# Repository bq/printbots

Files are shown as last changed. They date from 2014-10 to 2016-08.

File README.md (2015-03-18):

<table>
<tr>
<td>

</td>
</tr>
</table>

# BQ Printbots

In this repository you will find the source files for the **bq printbots**. If you are missing something, please do not hesitate to [file an issue on github](https://github.com/bq/printbots/issues)

En este repositorio se encuentran los ficheros fuente de los **Printbots de bq**. Si echas en falta algo, no dudes en [rellenar una tarea en github](https://github.com/bq/printbots/issues)

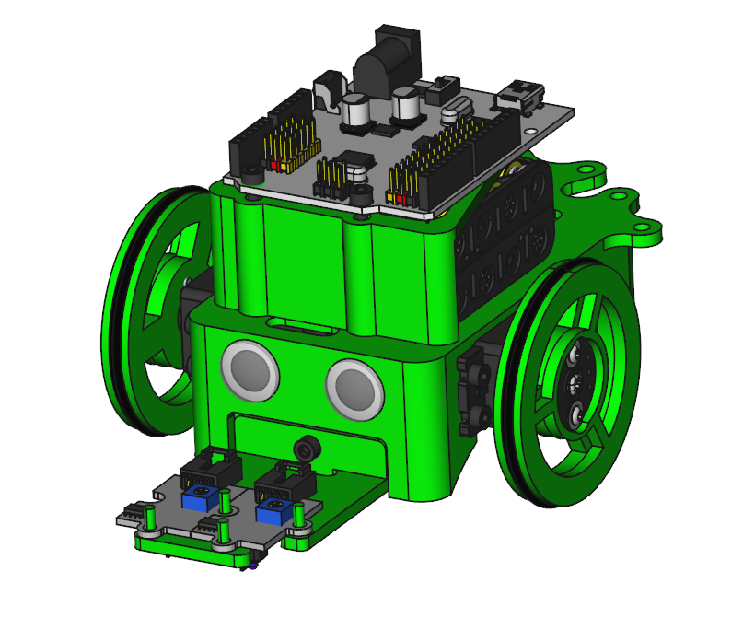
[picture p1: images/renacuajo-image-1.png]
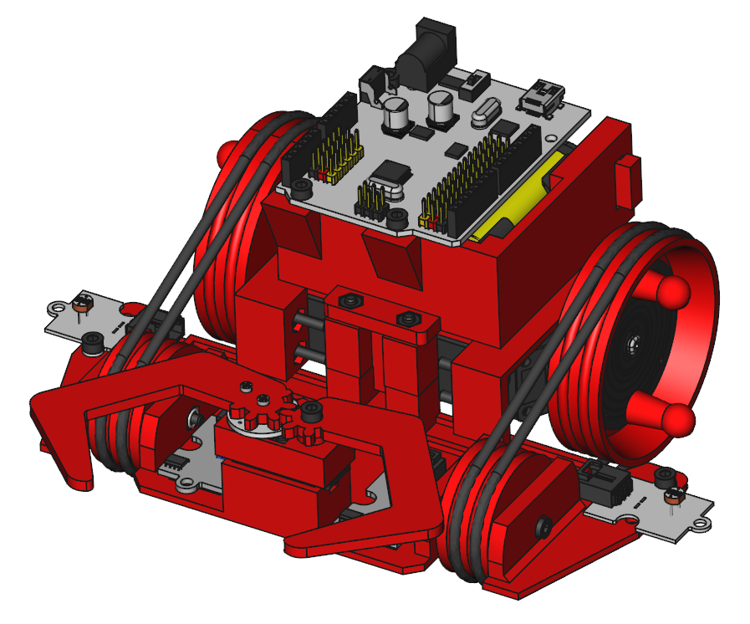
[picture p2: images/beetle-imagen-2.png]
 | 
:-------------: | :-------------:
[Printbot Renacuajo](http://diwo.bq.com/montaje-del-printbot-renacuajo/)|[Printbot Beetle](http://diwo.bq.com/product/kit-printbot-beetle/) 

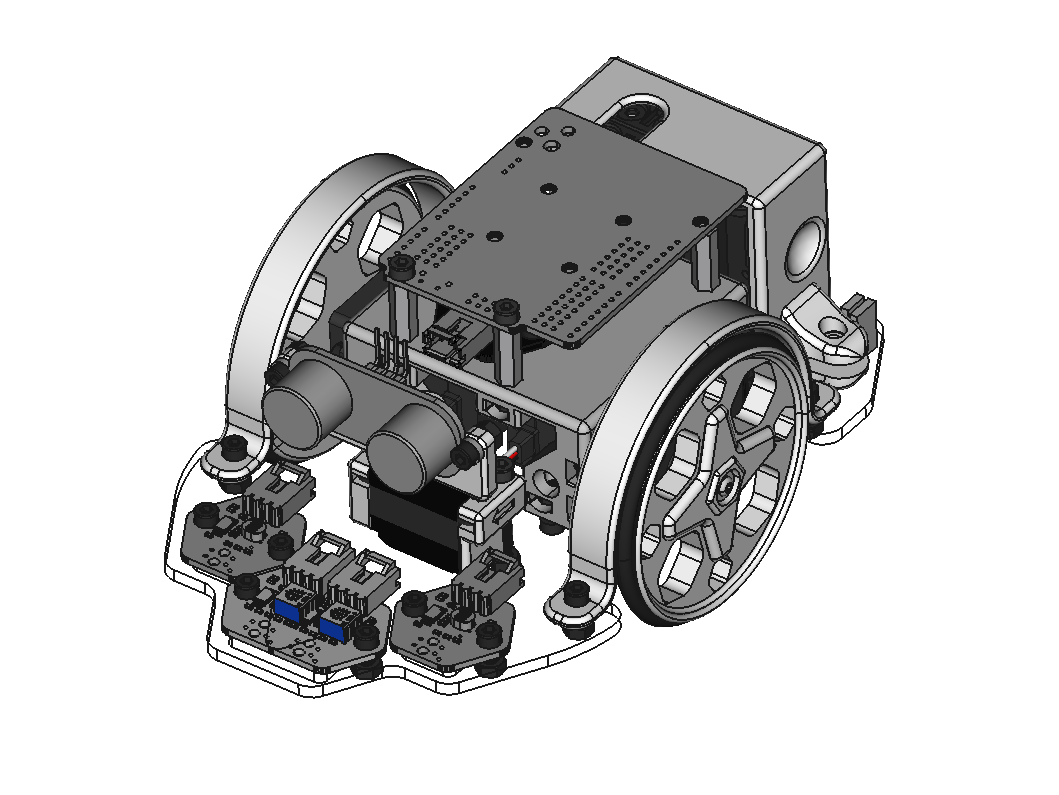
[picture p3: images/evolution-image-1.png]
 |
:-------------: | 
[Printbot Evolution]( http://diwo.bq.com/montaje-del-printbot-evolution/)|

# License 



All the printbots are licensed under a [Creative Commons Attribution-ShareAlike 4.0 International License](http://creativecommons.org/licenses/by-sa/4.0/). Please read the LICENSE files for more details.

Todos los printbots tienen la licencia [Creative Commons Attribution-ShareAlike 4.0 International License](http://creativecommons.org/licenses/by-sa/4.0/). Por favor, lea los ficheros LICENSE para más detalles

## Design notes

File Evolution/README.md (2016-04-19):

<p align="center">

</p>

<p align="center">
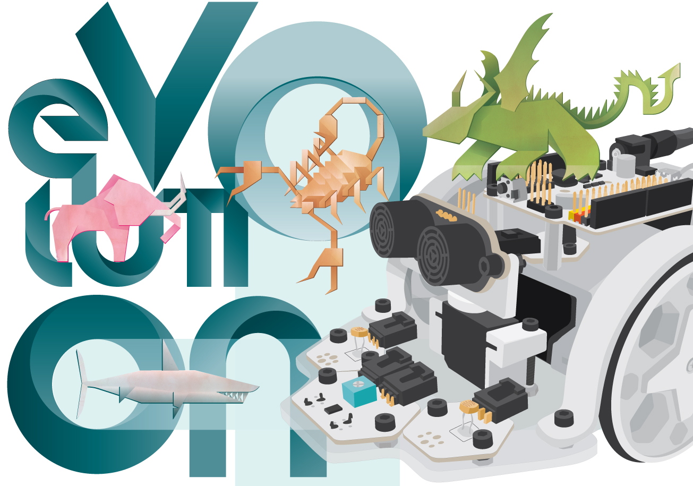
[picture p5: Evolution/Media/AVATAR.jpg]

</p>

# Printbot Evolution

<p align="center">
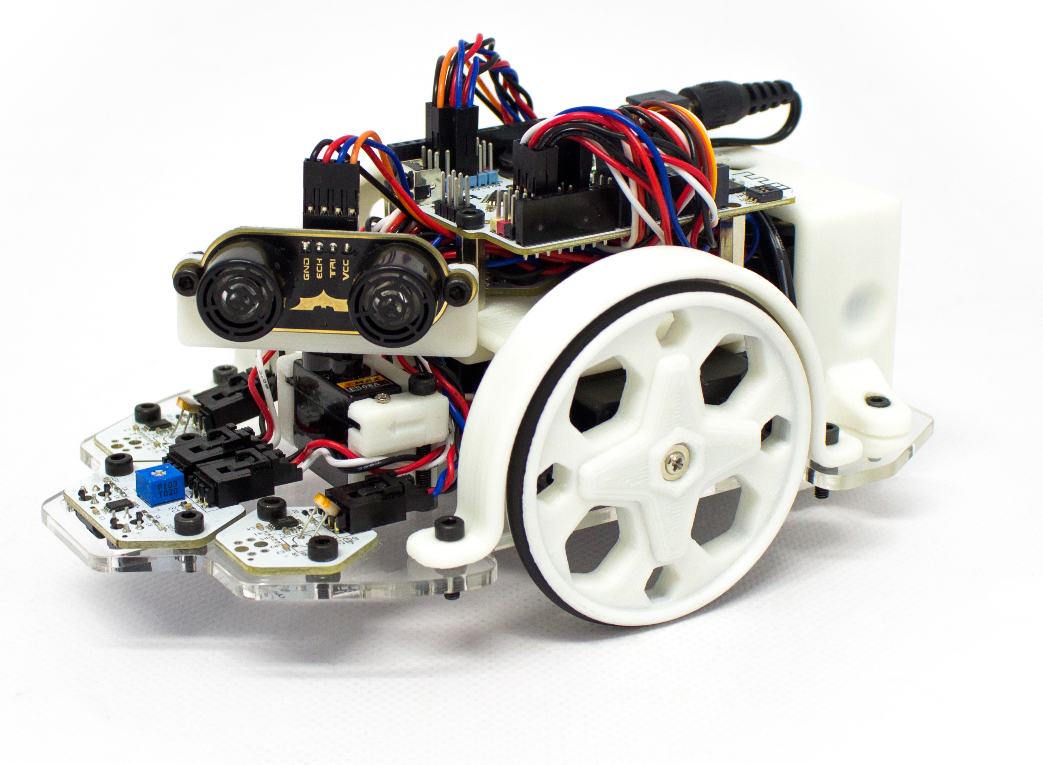
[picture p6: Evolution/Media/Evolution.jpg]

<div align="center"><i>Printbot Evolution V.1.0</i></div>
</p>

In this repository you will find the source files for the [bq Printbot Evolution](http://diwo.bq.com/montaje-del-printbot-evolution/). If you are missing something, please do not hesitate to [file an issue on github](https://github.com/bq/printbots/issues)

En este repositorio se encuentran los ficheros fuente del [Printbot  Evolution de bq](http://diwo.bq.com/montaje-del-printbot-evolution/). Si echas en falta algo, no dudes en [rellenar una tarea en github](https://github.com/bq/printbots/issues)

<p align="center">
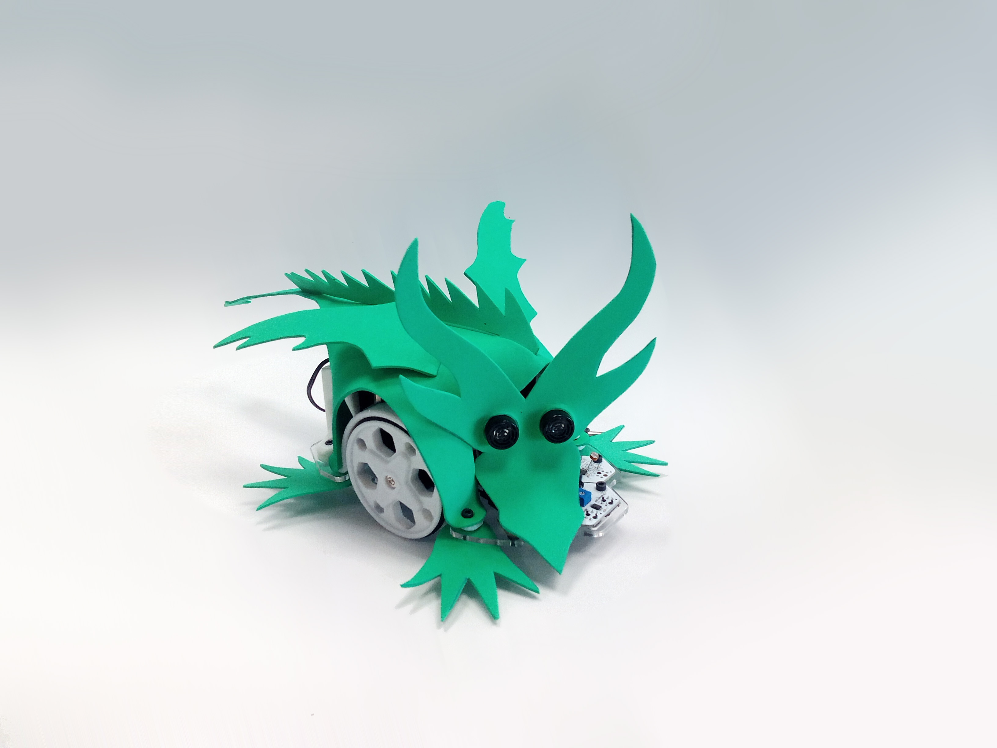
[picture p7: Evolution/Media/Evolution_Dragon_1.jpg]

<div align="center"><i>Printbot Evolution with Dragon Skin</i></div>
</p>

# Directory structure

 * `freecad`: Evolution source files in [FreeCAD](http://www.freecadweb.org/)

 * `stl`: Parts exported to stl. Ready for printing

 * `step`: Parts exported to step format

 * `Media` : Evolution images

 * `dxf` : .dxf files

 * `Skins_layout` : Skin layouts files

 * `addons` : New pieces and other stuff to expand the Evolution

 * `Evolution-BOM.ods`: Evolution Bill of Materials. Document for [LibreOffice](https://www.libreoffice.org/).

# Evolution Assembly in Freecad

In the Freecad folder there is an Assembly of the printbot Evolution. The source files for the vitamins (servos, board, nuts, bolts, etc) are available in the [Freecad part library](https://github.com/yorikvanhavre/FreeCAD-library)

# License

<p align="center">

</p>

This printbot is licensed under a [Creative Commons Attribution-ShareAlike 4.0 International License](http://creativecommons.org/licenses/by-sa/4.0/). Please read the LICENSE files for more details.

Este printbot tienen una licencia [Creative Commons Attribution-ShareAlike 4.0 International License](http://creativecommons.org/licenses/by-sa/4.0/). Por favor, lea los ficheros LICENSE para más detalles

# CREDITS

* **Pedro de Oro Martín**: Printbot original design and skins design; Dragon and Scorpion.
* **Federico Figueiredo de Sousa**: Skins design; Elephant and Shark.
* **Ana de Prado Navarrete**: Programming examples.
* **Sonia Verdú Calatayud and Leonor Sanahuja**: Layout of templates.
* **Julián Caro Linares**: Bumper design.
* **Jokin Lacalle**: Derivative acrylic base adapted for individuals IR.

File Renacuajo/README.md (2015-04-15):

<table>
<tr>
<td>

</td>
</tr>
</table>

# Printbot Renacuajo

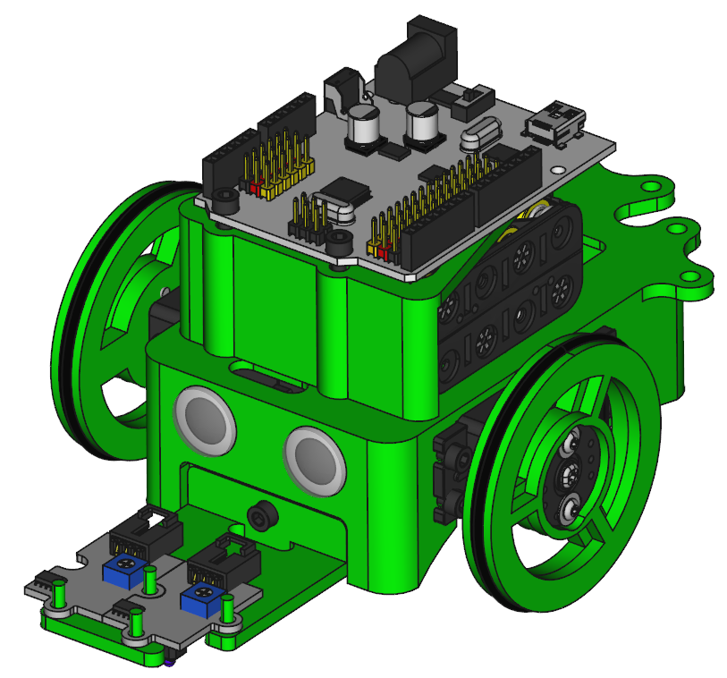
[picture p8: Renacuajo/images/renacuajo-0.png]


In this repository you will find the source files for the [bq Printbot Renacuajo](http://diwo.bq.com/montaje-del-printbot-renacuajo/). If you are missing something, please do not hesitate to [file an issue on github](https://github.com/bq/printbots/issues)

En este repositorio se encuentran los ficheros fuente del [Printbot Renacuajo de bq](http://diwo.bq.com/montaje-del-printbot-renacuajo/). Si echas en falta algo, no dudes en [rellenar una tarea en github](https://github.com/bq/printbots/issues)

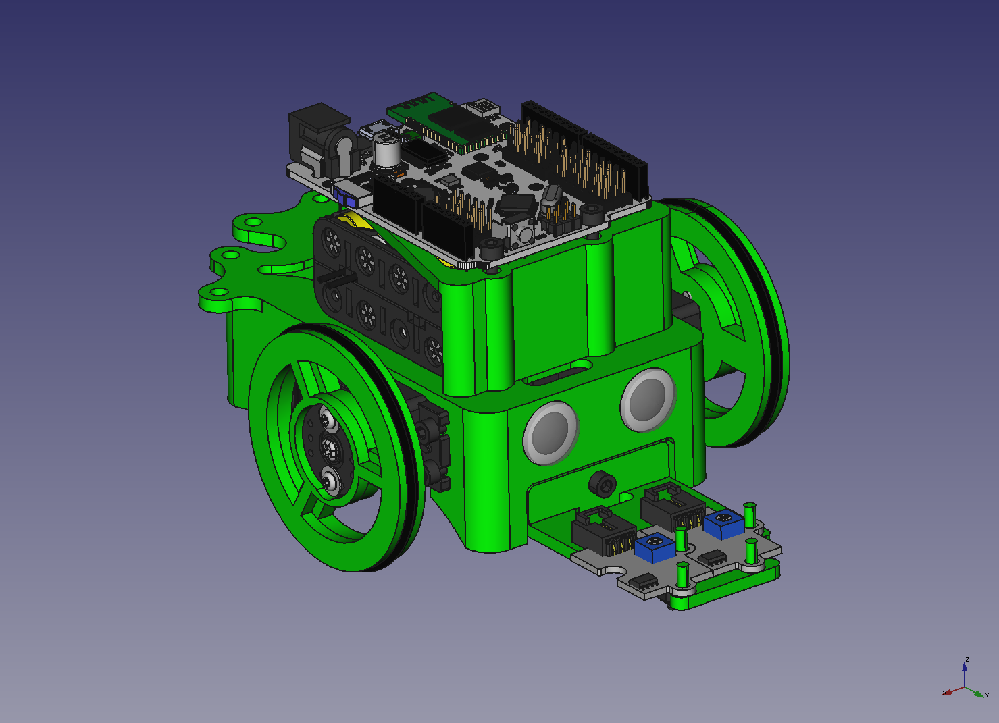
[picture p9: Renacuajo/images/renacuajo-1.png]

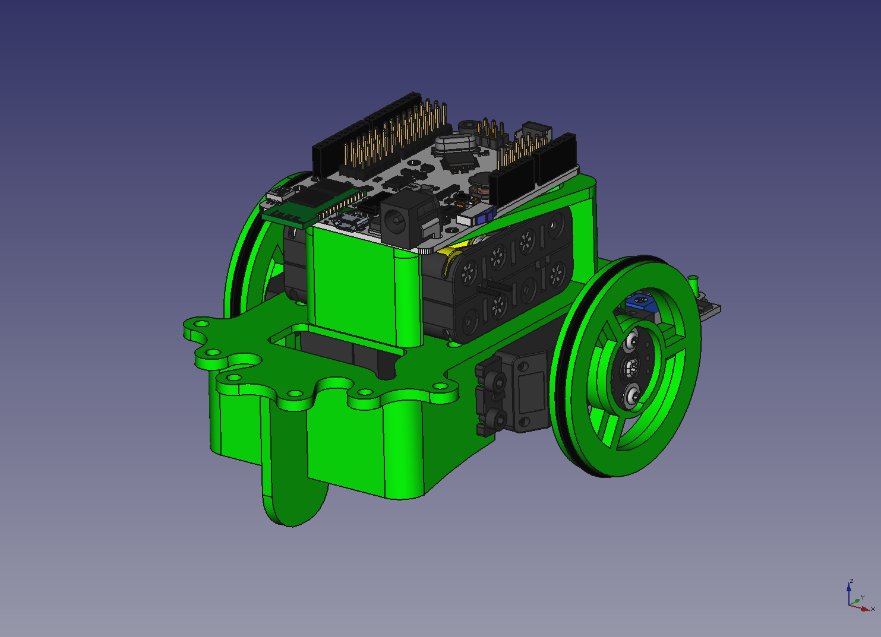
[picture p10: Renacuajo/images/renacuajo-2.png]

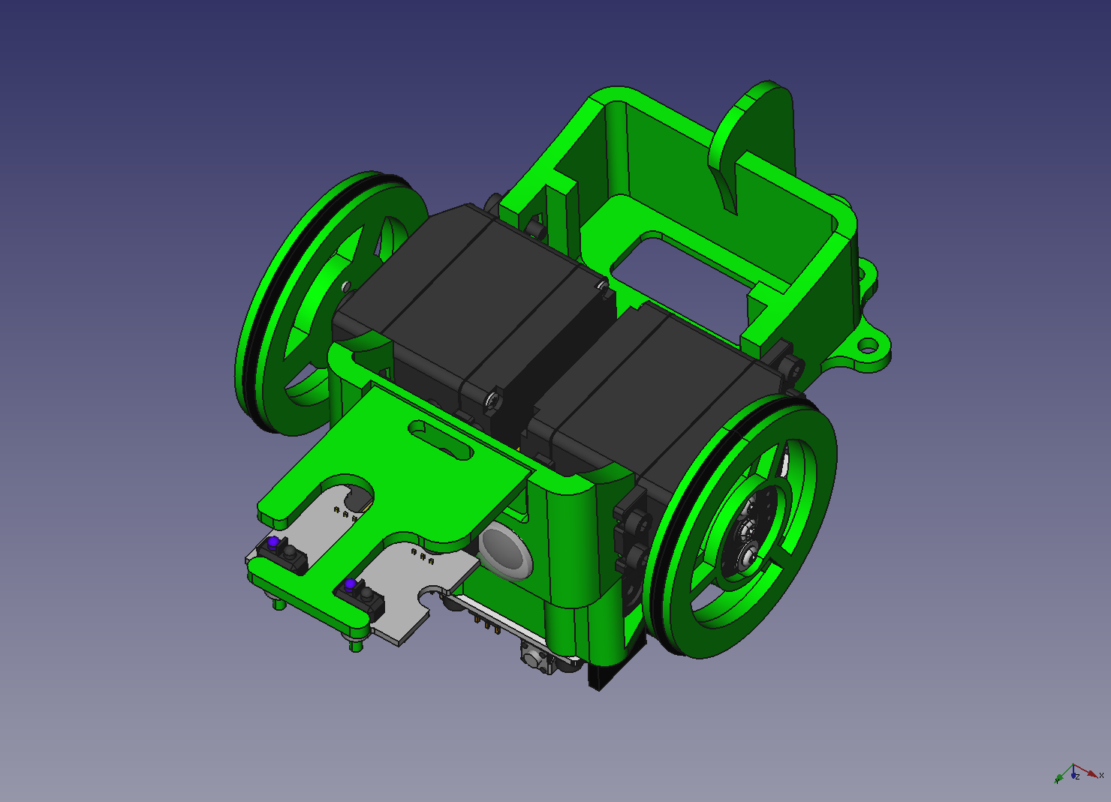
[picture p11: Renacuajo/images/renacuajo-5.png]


# Directory structure

 * `freecad`: Renacuajo source files in [FreeCAD](http://www.freecadweb.org/)

 * `stl`: Parts exported to stl. Ready for printing

 * `step`: Parts exported to step format

 * `images` : Renacuajo images

 * `renacuajo-BOM.ods`: Bettle Bill of Materials. Document for [LibreOffice](https://www.libreoffice.org/).

# Renacuajo Assembly in Freecad

In the Freecad folder there is an Assembly of the printbot Renacuajo. The source files for the vitamins (servos, board, nuts, bolts, etc) are available in the [Freecad part library](https://github.com/yorikvanhavre/FreeCAD-library)

  **All the source files for the parts in the assembly are available**

# Robopad++: Controlling the Robot from your android smartphone

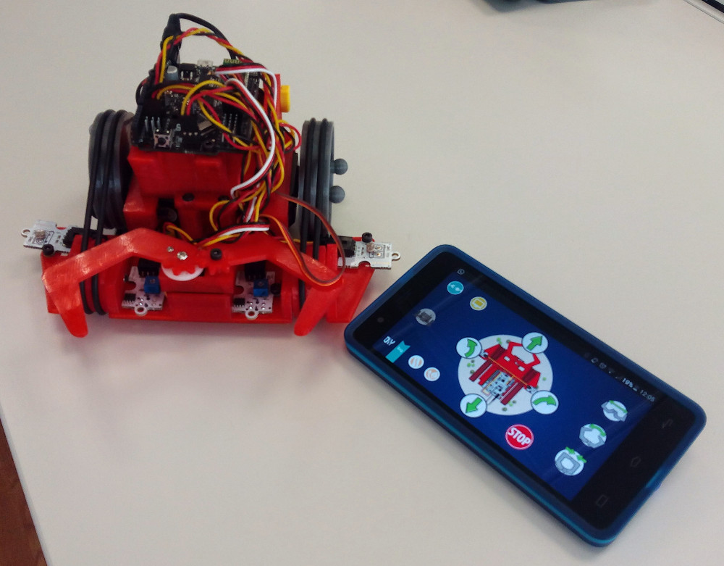
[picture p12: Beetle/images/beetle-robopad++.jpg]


The printbot Renacuajo can be controlled using your **smartphone**. You need a bluetooth module connected to the freaduino / Arduino board (or using the ZUM BT-328 which already include an embebbed bluetooth module)

  Install the [Robopad++](https://github.com/bq/robopad-plusplus) app available from the Google play store. It is open source, released under the GPL license. Check the [robopad++ github](https://github.com/bq/robopad-plusplus)

  You can find **more information on how to install and use this application** in [this Diwo post](http://diwo.bq.com/robopad-3/)

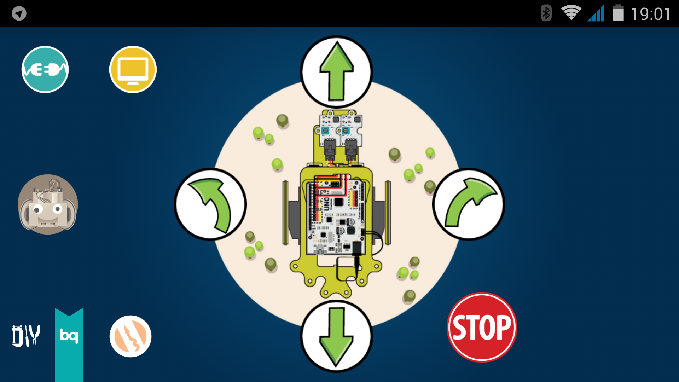
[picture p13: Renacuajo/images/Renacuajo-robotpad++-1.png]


# License 



This printbot is licensed under a [Creative Commons Attribution-ShareAlike 4.0 International License](http://creativecommons.org/licenses/by-sa/4.0/). Please read the LICENSE files for more details.

Este printbot tienen una licencia [Creative Commons Attribution-ShareAlike 4.0 International License](http://creativecommons.org/licenses/by-sa/4.0/). Por favor, lea los ficheros LICENSE para más detalles

# CREDITS
* **Miguel Angel de Frutos** (MAF): Original design
* The wheels have been derived from the [protobot](http://www.thingiverse.com/thing:18264), by **Alverto Valero**, **Mario Almagro** and **Nieves Cubo**
* **Pedro de Oro**: Sniffer for the ZUM double-IR sensor
* **Ana de Prado**: programming examples
* **Estefanía Sarasola**: Robopad++ app
* **Juan Gonzalez** (Obijuan): Migration to freecad. Assembly in Freecad

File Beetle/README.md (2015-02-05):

<table>
<tr>
<td>

</td>
</tr>
</table>

# Printbot Beetle



In this repository you will find the source files for the [bq Printbot Beetle](http://diwo.bq.com/product/kit-printbot-beetle/). If you are missing something, please do not hesitate to [file an issue on github](https://github.com/bq/printbots/issues)

En este repositorio se encuentran los ficheros fuente del [Printbot Beetle de bq](http://diwo.bq.com/product/kit-printbot-beetle/). Si echas en falta algo, no dudes en [rellenar una tarea en github](https://github.com/bq/printbots/issues)

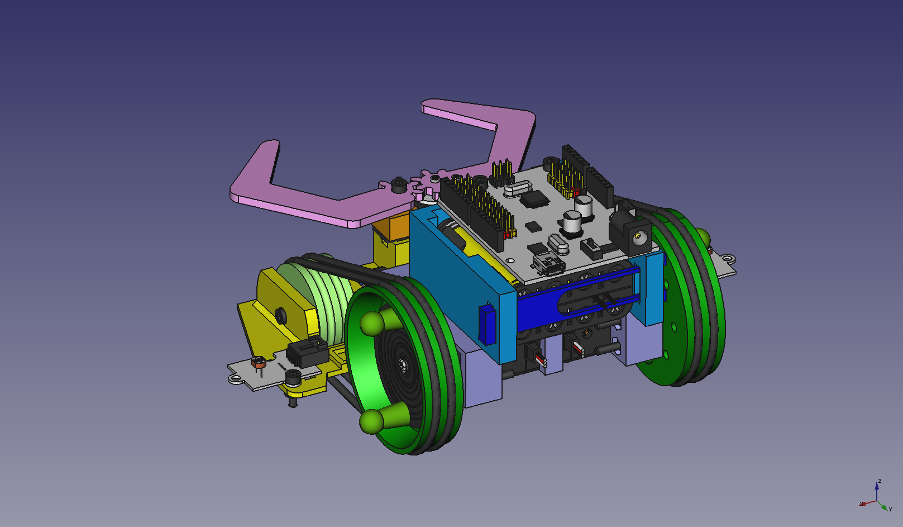
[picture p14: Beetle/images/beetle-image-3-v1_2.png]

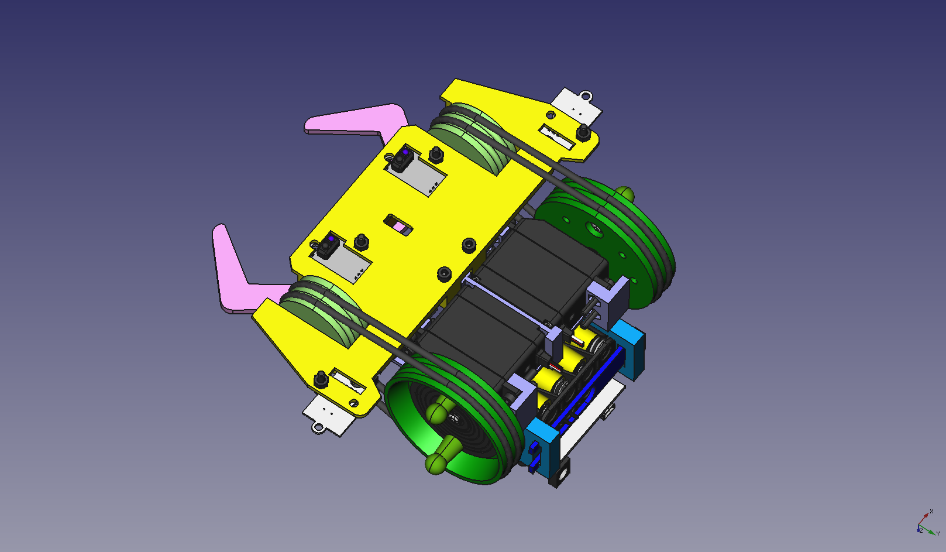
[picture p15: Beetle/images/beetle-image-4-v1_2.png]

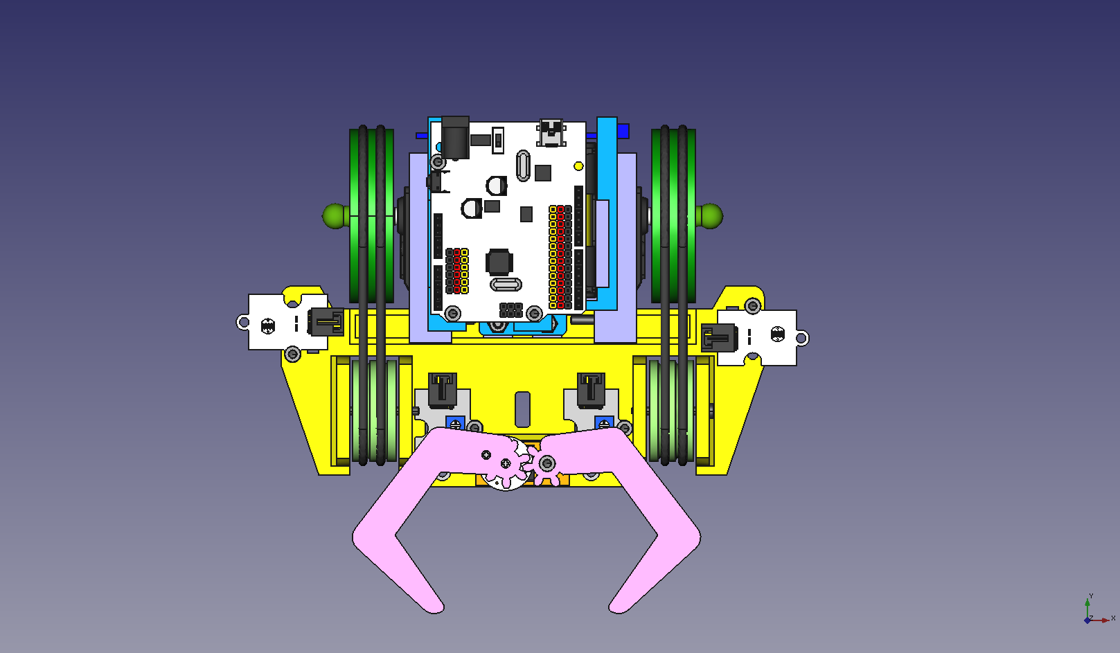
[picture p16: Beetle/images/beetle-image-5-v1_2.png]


# Directory structure

 * `legacy`: Older versions

 * `freecad`: Beetle source files in [FreeCAD](http://www.freecadweb.org/)

 * `stl`: Parts exported to stl. Ready for printing

 * `step`: Parts exported to step format

 * `sw-examples`: Programming examples (for Arduino compatible boards)

 * `images` : Beetle images

 * `beetle-BOM.ods`: Bettle Bill of Materials. Document for [LibreOffice](https://www.libreoffice.org/).

# Beetle Assembly in Freecad

In the Freecad folder there is an Assembly of the printbot Beetle. The source files for the vitamins (servos, board, nuts, bolts, etc) are available in the [Freecad part library](https://github.com/yorikvanhavre/FreeCAD-library)

  **All the source files for the parts in the assembly are available**

# Robopad++: Controlling the Robot from your android smartphone



The printbot beetle can be controlled using your **smartphone**. You need a bluetooth module connected to the freaduino / Arduino board (or using the ZUM BT-328 which already include an embebbed bluetooth module)

  Install the [Robopad++](https://github.com/bq/robopad-plusplus) app available from the Google play store. It is open source, released under the GPL license. Check the [robopad++ github](https://github.com/bq/robopad-plusplus)

  You can find **more information on how to install and use this application** in [this Diwo post](http://diwo.bq.com/robopad-3/)

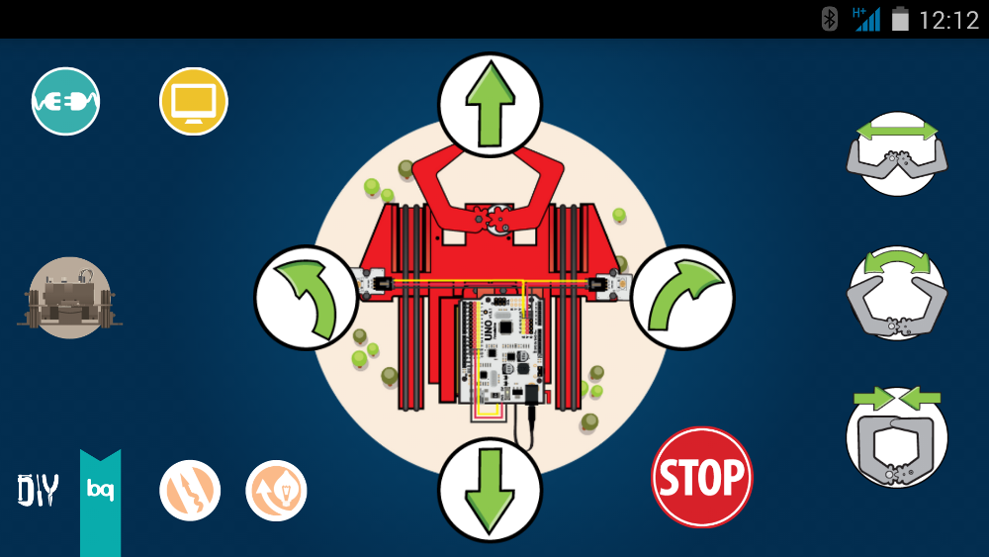
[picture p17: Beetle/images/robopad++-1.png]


# License 



This printbot is licensed under a [Creative Commons Attribution-ShareAlike 4.0 International License](http://creativecommons.org/licenses/by-sa/4.0/). Please read the LICENSE files for more details.

Este printbot tienen una licencia [Creative Commons Attribution-ShareAlike 4.0 International License](http://creativecommons.org/licenses/by-sa/4.0/). Por favor, lea los ficheros LICENSE para más detalles

# CREDITS
* **Jon Goitia**: Original design (Beetle V1.0). It is a derivative of his own [mini rover printbot](http://www.thingiverse.com/thing:18392)
* **David Sanchez**: migration to freecad of the rear wheels and servo-screw-cover. Adaptation to Beetle v1.2
* **Ana de Prado**: programming examples
* **Estefanía Sarasola**: Robopad++ app
* **Juan Gonzalez** (Obijuan): Migration to freecad of the beetle parts. Adaptation to v1.2. New assembly in Freecad

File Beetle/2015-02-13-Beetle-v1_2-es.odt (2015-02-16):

Printbot Beetle 1.2:

Cambios realizados


13 - Feb – 2015

Juan González Gómez (Obijuan)

# Modificaciones realizadas en el printbot Beetle v1.2

## Pieza frontal

1.- Añadido segundo taladro de los sensores IR

2.- Modificadas las huellas donde encajan los IR para que entren bien

3.- Agrandado el hueco de las tuercas empotradas para que entren bien

4.- Agrandado taladro de enganche de la pieza de los servos. Ahora los tornillos entran muy fácilmente

5.- Refuerzos en las paredes verticales de soporte de las ruedas y mini-servo

6.- Nervio central para reforzar la estructura

7.- Slot para pasar el cable del miniservo por debajo del chásis y ocultarlo

8.- Adelantado el hueco del miniservo para que el tornillo no coincida con el eje de la rueda. Así es más fácil colocar los tornillos (de la rueda y sensor) en cualquier orden.

(Ver figura 1)

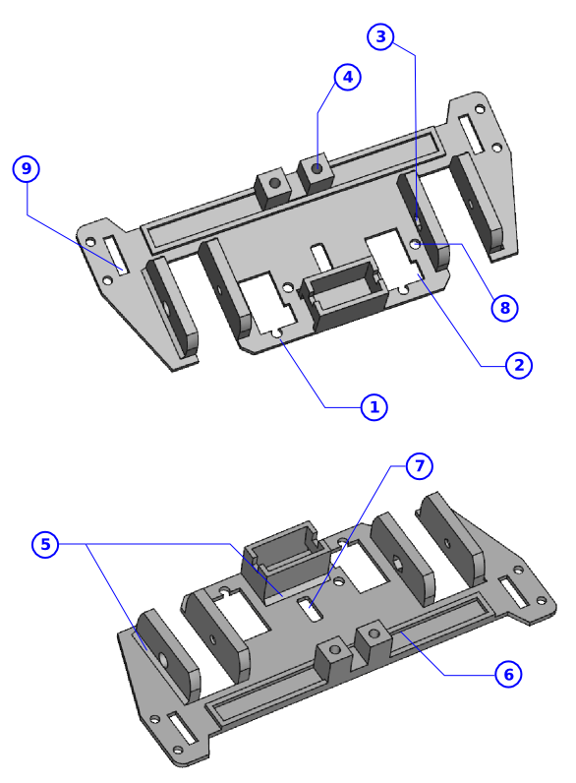
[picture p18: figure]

Figura 1: Pieza frontal de Beetle v1.2

## Pieza trasera de servos

1.- Agrandado el alojamiento de las tuercas. Ahora entran perfectamente

2.- Cambiada la orientación del alojamiento de las tuercas. Se imprime mucho mejor

3.- Eliminado el frontal donde van los tornillos de los servos: Ahora aprisionan el servo directamente contra la pieza, quedando todo más compacto. Se eliminan tensiones que hacían que se pudiese romper esa parte

4.- Agrandados los taladros de los tornillos de anclaje a la parte frontal. Ahora los tornillos entran muy suavemente

5.- Añadido dibujo con la orientación de los servos. Esto facilita el montaje

6.- Modificada la anchura del anclaje para que entre más suavemente en el hueco de la pieza frontal

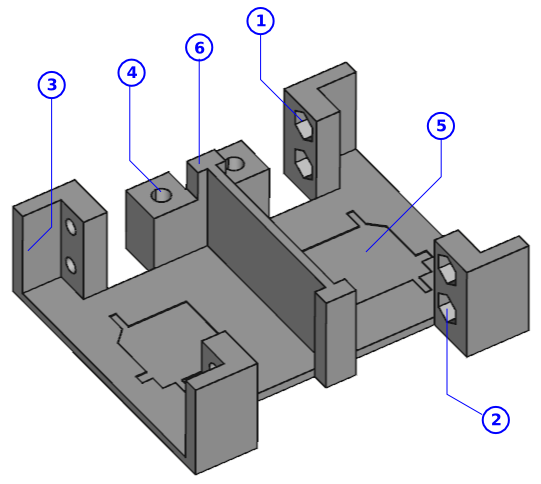
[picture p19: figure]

Figura 2: Pieza trasera con los servos

# Pieza soporte del portapilas

# 1.- Agrandados los taladros de amarre a la pieza de los servos. Ahora entra suavemente

# 2.- Agrandados los huecos de las tuercas para entren suavemente

# 3, 4.- Hueco en las partes derecha e izquierda de la pieza para que entren los cables por la parte interior. De esta forma quedan ocultos y se mejora las estética del robot

# 5.- Agrandados los diámetros de los taladros para los tornillos de amarre de la electrónica. Ahora entran más fácilmente

# 6.- Mayor grosor en las paredes del slot para que se impriman con mayor calidad

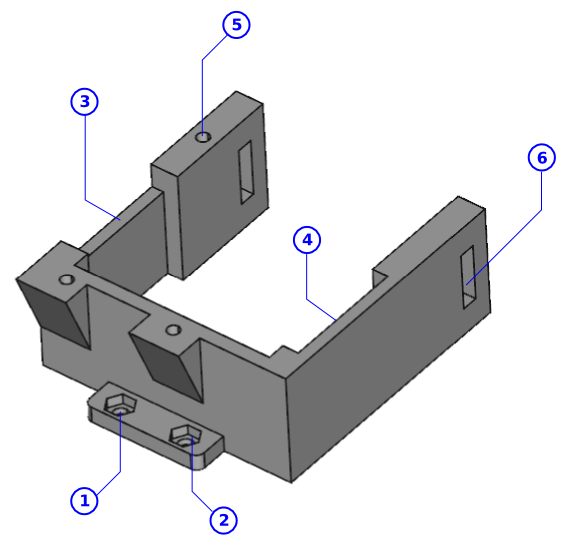
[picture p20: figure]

# Figura 3: Soporte para el portapilas

# Pieza de soporte del miniservo

1.- Agrandados los taladros de los tornillos para que entren mejor y no se deteriore la cabeza

2.- Ajustada la distancia entre los tornillos para atornillar mejor el servo. Antes los tornillos entraban ligeramente torcidos

3.- Agrandado el tamaño del hueco de la tuerca para entre sin problemas

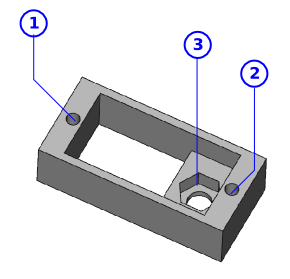
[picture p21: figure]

Figura 4: Soporte del miniservo

# Rueda trasera

1.- Taladros agrandados para que los tornillos de los servos entren más suavemente

2.- Añadido un cierre en los huecos para las cabezas de los tornillos. De esta manera se mejora la impresión

(Ver figura 5)

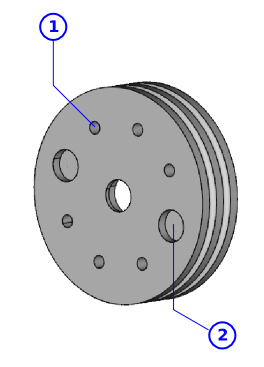
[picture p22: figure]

Figura 6: Rueda trasera

# Cubre tornillos

1.- Agrandado el taladro para que se enrosque sin hacer apenas fuerza en el tornillos

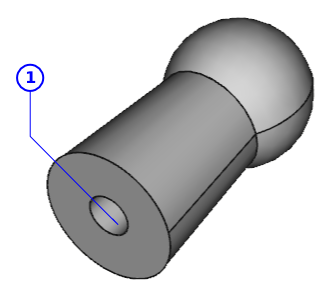
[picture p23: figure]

Figura 7: Rueda trasera

# Otras mejoras

## Cableado

El cableado en la versión 1.2 queda mucho más escondido. Los cables van por debajo del robot y llegan a la tarjeta entrando por el hueco del portapilas. En la versión anterior se hacía directamente por la parte frontal del robot.

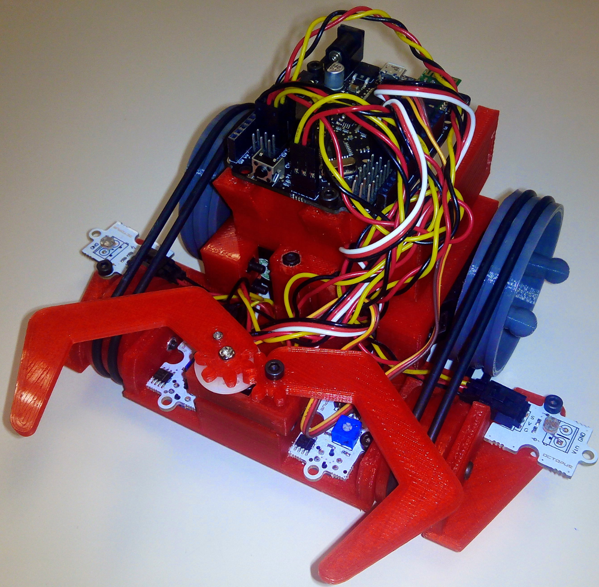
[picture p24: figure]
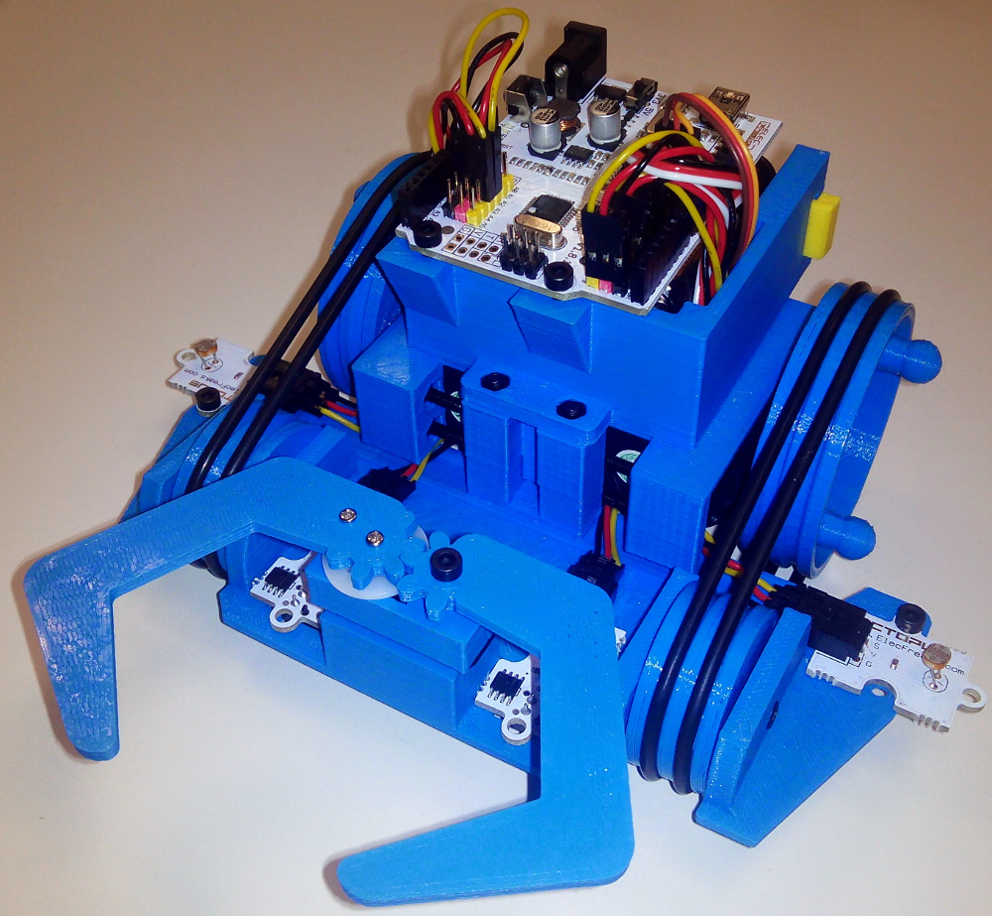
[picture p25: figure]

Cableado en beetle 1.0 | Cableado en beetle 1.2

## Diseño 3D migrado a Freecad

Todas las piezas se han migrado a Freecad, que es una aplicación libre de diseño 3D, multiplataforma. Ahora es más fácil para la gente poder ver las piezas virtuales y modificarlas. También se ha realizado el ensamblado 3D, que sirve de ayuda para ver cómo se construye el robot

Están disponibles en el repositorio oficial de bq en github:

https://github.com/bq/printbots/tree/master/Beetle

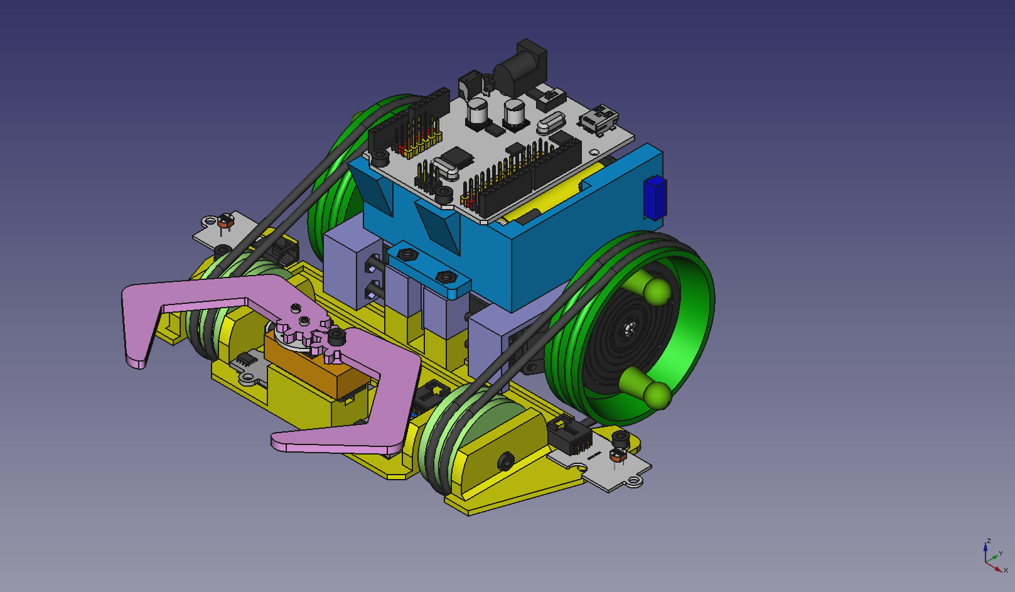
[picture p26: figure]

Figura 8: Ensamblaje del printbot beetle en Freecad

# Conclusiones

- Mayor facilidad en el montaje
- Cableado más limpio y estético
- Migración del modelo a Freecad
- Ahora la comunidad puede evolucionar el modelo más fácilmente

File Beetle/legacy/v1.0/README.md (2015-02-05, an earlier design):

Original Beetle (v1.0), by Jon Goitia
It was designed in [Openscad](http://www.openscad.org/)

# Directory structure

 * `doc`: Assembly manuals

 * `scad`: Beetle source files in [Openscad](http://www.openscad.org/)

 * `stl`: Parts exported to stl. Ready for printing

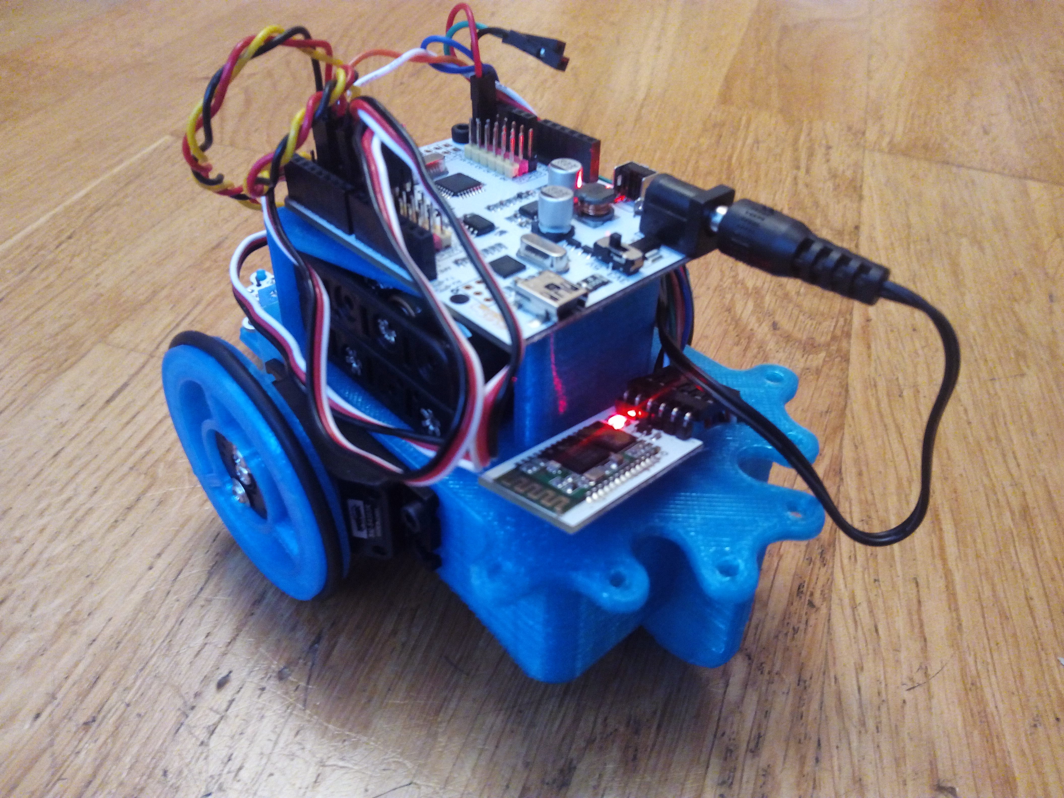
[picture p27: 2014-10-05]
Renacuajo/images/renacuajo-8.jpg

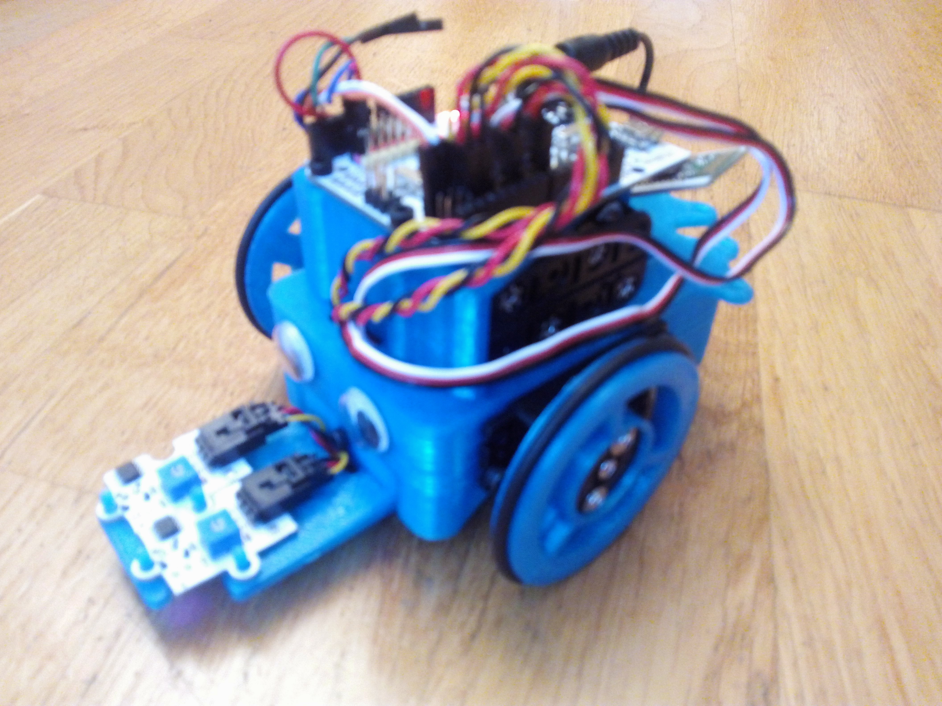
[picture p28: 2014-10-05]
Renacuajo/images/renacuajo-7.jpg

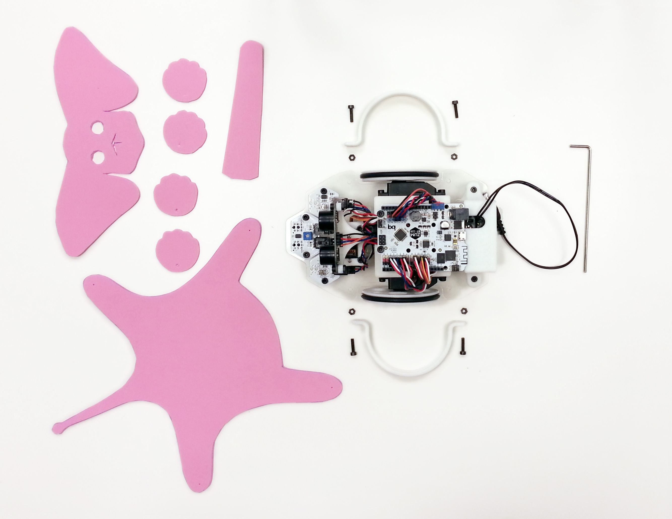
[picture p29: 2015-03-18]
Evolution/Media/Evolution_Elefante_2.jpg

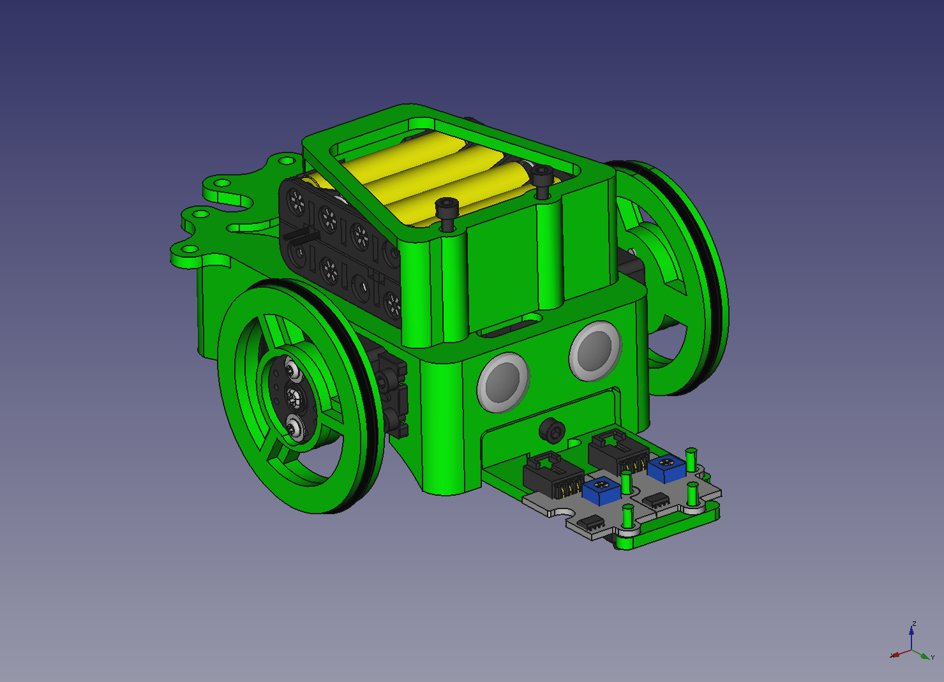
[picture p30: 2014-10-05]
Renacuajo/images/renacuajo-3.png

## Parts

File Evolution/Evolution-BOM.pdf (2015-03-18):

Renacuajo BOM

Description | Quantity
M3x8 Screw - DIN-912 8.8 | 26
M3x8 Screw - DIN-912 8.8 | 6
M3x8 Screw - DIN-912 8.8 | 2
M3 Nut – DIN 934 Class 8 | 34
Battery holder for 4 AA | 1
Continuous-rotation servos | 2
Mini-servos | 1
ZUM BT-328 | 1
ZUMbloq PhotoResitor Light Sensor | 2
ZUMbloq Buzzer | 1
Bat US Sensor | 1
ZUMbloq InfraRed Hunt 2 Sensor | 1
Cable USB | 1
Hexagonal metal spacer 15mm with M3 on one side | 4
O-Ring (Junta Tórica) DI 56 mm, d 4mm Black Ref H1899 | 2
EVOLUTION - Cuerpo | 1
| 1
| 2
| 2
| 1
| 1
| 2
| 1

EVOLUTION - Portapilas
EVOLUTION - Rueda
EVOLUTION - Tapa rueda
EVOLUTION- Sujeta miniservo EVOLUTION - Sujeta ultrasonido EVOLUTION - Guardabarros
EVOLUTION - Base de metacrilato 3mm

Renacuajo BOM

Units | Comments
PCs
PCs
PCs
PCs
PCs
PCs
PCs
PCs Compatibility with Arduino boards PCs
PCs
PCs
PCs
PCs
PCs
PCs
PCs | Printed part
PCs | Printed part
PCs | Printed part
PCs | Printed part
PCs | Printed part
PCs | Printed part
PCs | Printed part
PCs | Printed part or Laser cut

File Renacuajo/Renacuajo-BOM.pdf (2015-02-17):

Renacuajo BOM

Part Number | Description | Quantity | Units | Comments
| Main chassis | 1 | PCs | Printable part
| Wheel | 2 | PCs | Printable part
| Sniffer | 1 | PCs | Printable part
| Battery holder | 1 | PCs | Printable part
| M3x10 ISO4762 bolt | 15 | PCs
| M3x40 ISO4762 bolt | 2 | PCs
| M3 Nuts | 17 | PCs
| Servo SM-S4303R | 2 | PCs
| Octopus IR sensors | 2 | PCs
| O-ring Ø3 section, Ø50 | 4 | PCs
| Battery pack holder | 1 | PCs | For 8 AAA batteries
| AAA batteries | 8 | PCs
| Freaduino uno board | 1 | PCs
| Eyes | 2 | PCs

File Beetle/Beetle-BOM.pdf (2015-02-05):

Beetle BOM

Part Number | Description | Quantity | Units | Comments
| Front frame | 1 | PCs | Printable part
| Claw pincer servo | 1 | PCs | Printable part
| Claw pincer idler | 1 | PCs | Printable part
| Claw miniservo box | 1 | PCs | Printable part
| Frame rear servos | 1 | PCs | Printable part
| Battery pack holder | 1 | PCs | Printable part
| battery pack clip | 1 | PCs | Printable part
| Front wheel | 2 | PCs | Printable part
| Rear wheel | 2 | PCs | Printable part
| Servo screw cover | 4 | PCs | Printable part
| M3x10 ISO4762 bolt | 7 | PCs
| M3x12 ISO4762 bolt | 1 | PCs | Claw pincer idler shaft
| M3x16 ISO4762 bolt | 8 | PCs | Attaching rear Servos
| M3x25 ISO476 bolt | 2 | PCs | Front wheel shafts
| M3x35 ISO476 bolt | 2 | PCs
| M3 nuts | 17 | PCs
| M3 Nylock nut | 3 | PCs
| Servo SM-S4303R | 2 | PCs
| Miniservo ES08A | 1 | PCs | For Claw pincer
| Octopus IR sensors | 2 | PCs
| Octopus LDR sensors | 2 | PCs
| O-ring Ø3 section, Ø85 | 4 | PCs
| Battery pack holder | 1 | PCs | For 8 AAA batteries
| AAA batteries | 8 | PCs
| Freaduino uno board | 1 | PCs

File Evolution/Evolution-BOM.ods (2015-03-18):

Description | Quantity | Units | Comments
M3x8 Screw - DIN-912 8.8 | 26 | PCs
M3x8 Screw - DIN-912 8.8 | 6 | PCs
M3x8 Screw - DIN-912 8.8 | 2 | PCs
M3 Nut – DIN 934 Class 8 | 34 | PCs
Battery holder for 4 AA | 1 | PCs
Continuous-rotation servos | 2 | PCs
Mini-servos | 1 | PCs
ZUM BT-328 | 1 | PCs | Compatibility with Arduino boards
ZUMbloq PhotoResitor Light Sensor | 2 | PCs
ZUMbloq Buzzer | 1 | PCs
Bat US Sensor | 1 | PCs
ZUMbloq InfraRed Hunt 2 Sensor | 1 | PCs
Cable USB | 1 | PCs
Hexagonal metal spacer 15mm with M3 on one side | 4 | PCs
O-Ring (Junta Tórica) DI 56 mm, d 4mm Black Ref H1899 | 2 | PCs
EVOLUTION - Cuerpo | 1 | PCs | Printed part
EVOLUTION - Portapilas | 1 | PCs | Printed part
EVOLUTION - Rueda | 2 | PCs | Printed part
EVOLUTION - Tapa rueda | 2 | PCs | Printed part
EVOLUTION- Sujeta miniservo | 1 | PCs | Printed part
EVOLUTION - Sujeta ultrasonido | 1 | PCs | Printed part
EVOLUTION - Guardabarros | 2 | PCs | Printed part
EVOLUTION - Base de metacrilato 3mm | 1 | PCs | Printed part or Laser cut

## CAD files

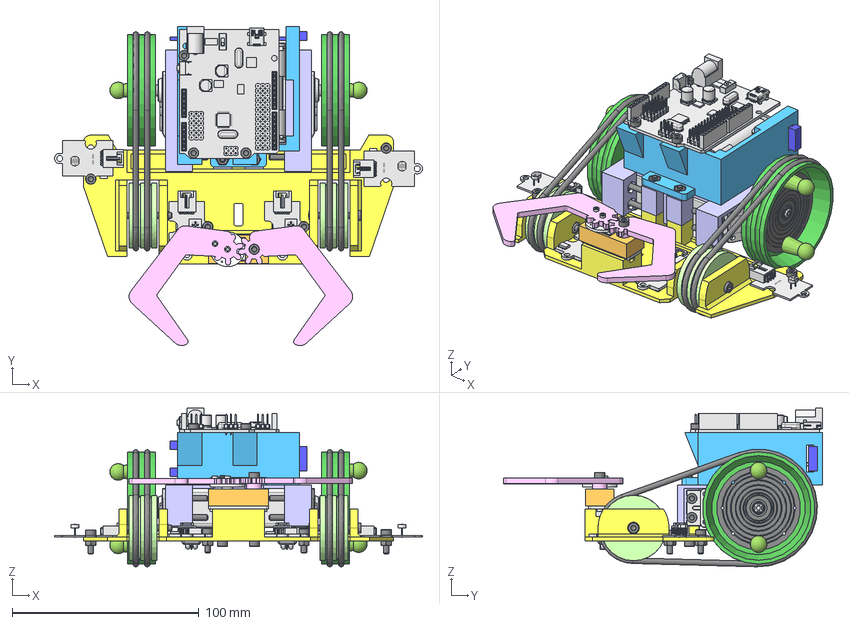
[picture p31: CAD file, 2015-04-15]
Beetle/freecad/Assembly.fcstd
196.8 x 170.6 x 84.9 mm
Nyloc-nut-M3
Nyloc-nut-M004
front-right-wheel
front-left-wheel
M3x25-bolt-iso-4762-1
M3x25-bolt-iso-4762-002
octopus-IR-sensor-1
M3x10-bolt-iso-4762-1
M3-nut-1
octopus-IR-sensor-2
M3x10-bolt-iso-4762-002
M3-nut-002
octopus-IR-LDR-sensor-1
M3x10-bolt-iso-4762-003
M3-nut-003
octopus-IR-LDR-sensor-002
M3x10-bolt-iso-4762-004
M3-nut-004
frame-front
Emax-es08A-final
claw-miniservo-box
Nyloc-nut-M005
screw-2x7.5mm-1
screw-2x7.5mm-002
servo-rounded-horn2
claw-pencil-servo
screw-1.7x6.2mm
screw-2x7.5mm-003
M3x10-bolt-iso-4762-005
claw-pincel-free
frame-rear-servos-part
Servo-SM-S4303R
Servo-SM-S4303R001
M3-nut-005
M3-nut-006
M3-nut-007
M3-nut-008
M3-nut-009
M3-nut-010
M3-nut-011
M3-nut-012
M3x16-bolt-iso-4762-1
M3x16-bolt-iso-4762-2
M3x16-bolt-iso-4762-003
M3x16-bolt-iso-4762-004
M3x16-bolt-iso-4762-005
M3x16-bolt-iso-4762-006
M3x16-bolt-iso-4762-007
M3x16-bolt-iso-4762-008
M3-nut-013
M3-nut-014
M3x35-bolt-iso-4762-1
M3x35-bolt-iso-4762-002
battery-pack-clip
battery-holder
batteries
battery-pack-holder-part
Wheel-rear002
servo-screw-003
servo-Shaft-screw-002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

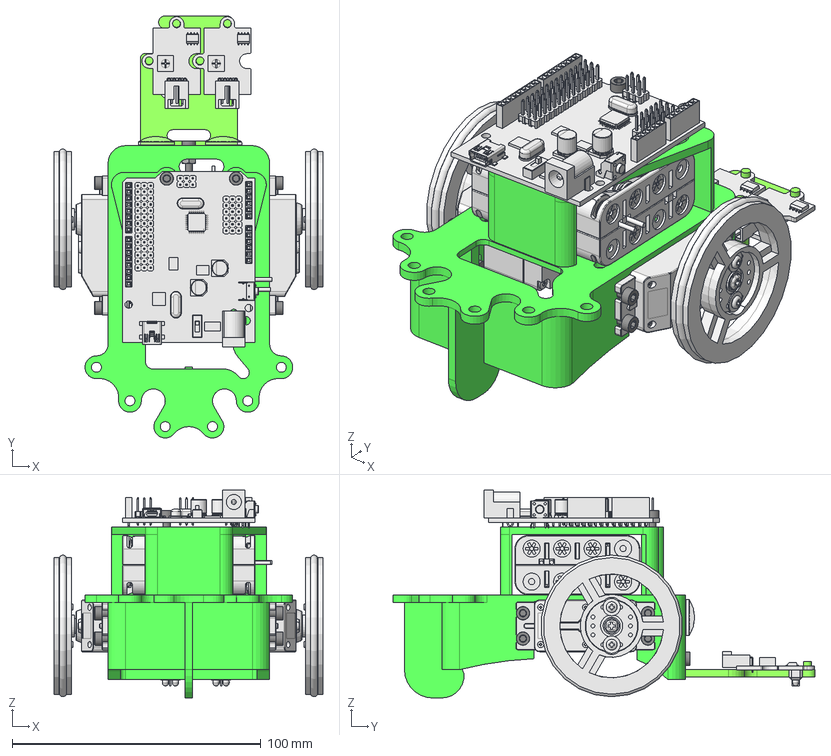
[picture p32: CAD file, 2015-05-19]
Renacuajo/freecad/renacuajo-assembly.fcstd
108.1 x 169.8 x 83.7 mm
renacuajo-chassis
octopus-IR-sensor-left
M3x10-sniffer-bolt
M3-sniffer-nut
octopus-IR-sensor-right
sniffer-base
Right-wheel
left-wheel
Shaft-screw-left
Shaft-screw-right
Servo-SM-S4303R-left
Servo-SM-S4303R-right
nut1
nut002
nut003
nut004
nut005
nut006
nut008
nut07
M3x10-servo-1
M3x10-servo-002
M3x10-servo-003
M3x10-servo-004
M3x10-servo-006
M3x10-servo-007
M3x10-servo-008
M3x10-servo-5
battery-holder
M3x40-bolt1
M3x40-bolt002
nut009
nut010
battery-pack
eye-base
black-eye
eye-cover
eye-base001
black-eye001
eye-cover001
freaduino-uno

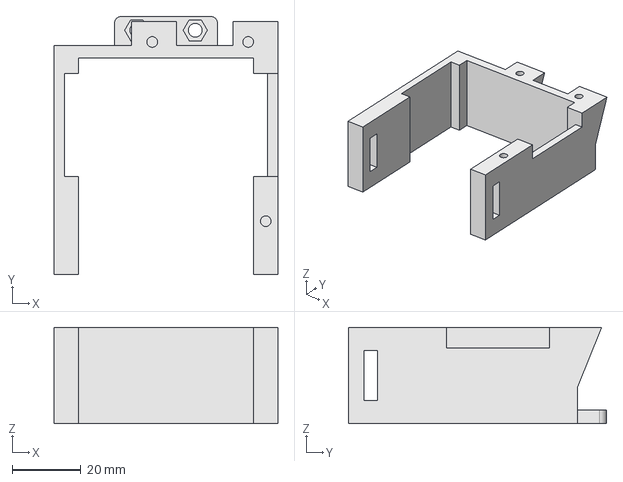
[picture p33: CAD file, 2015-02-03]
Beetle/step/battery-pack-holder.step
65.0 x 75.0 x 28.0 mm

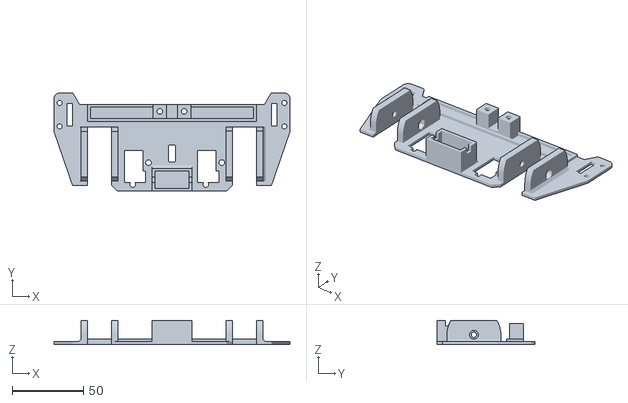
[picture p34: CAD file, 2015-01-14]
Beetle/stl/front-frame.stl
166.0 x 69.0 x 17.0

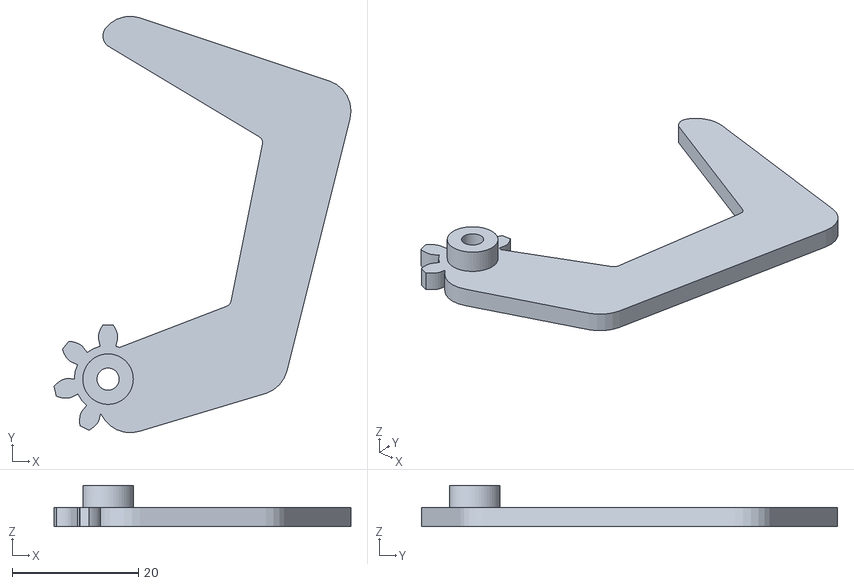
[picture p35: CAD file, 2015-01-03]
Beetle/stl/orig/claw_pincer_free.stl
47.1 x 66.0 x 6.50

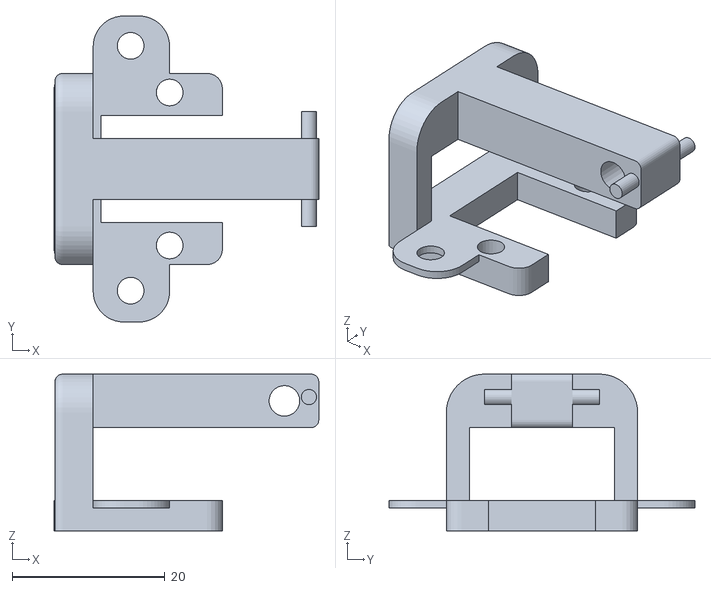
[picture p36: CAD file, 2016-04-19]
Evolution/addons/bumper/stl/final_bumper_holder_evolution.stl
34.6 x 40.0 x 20.5

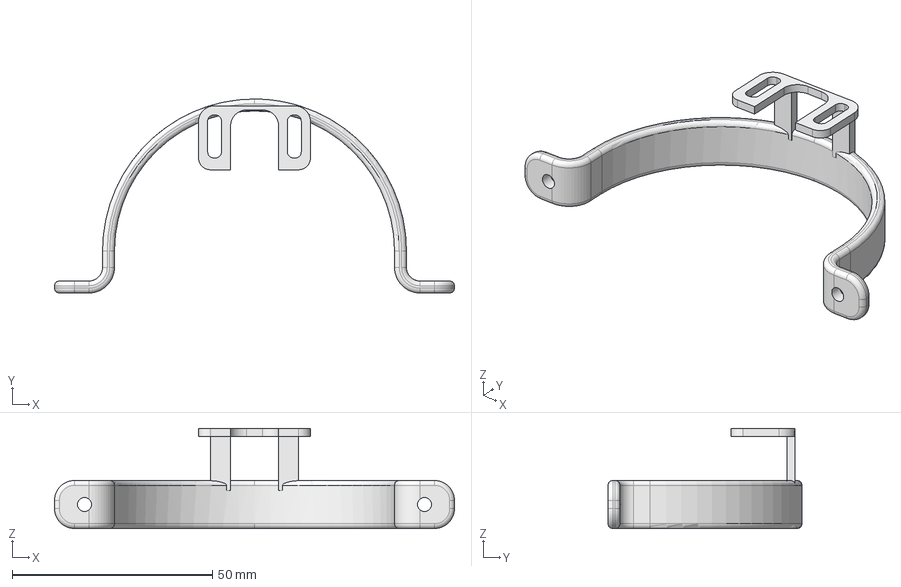
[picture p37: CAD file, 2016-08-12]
Evolution/addons/guardabarros_con_sensor/freecad/guardabarros_ir_adaptador_evolution_up.fcstd
100.0 x 48.5 x 25.0 mm

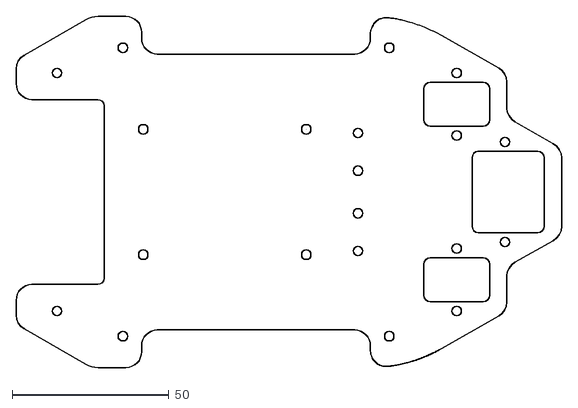
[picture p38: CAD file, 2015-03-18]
Evolution/dxf/Evolution_acrylic_3mm_base.dxf
174.0 x 112.0

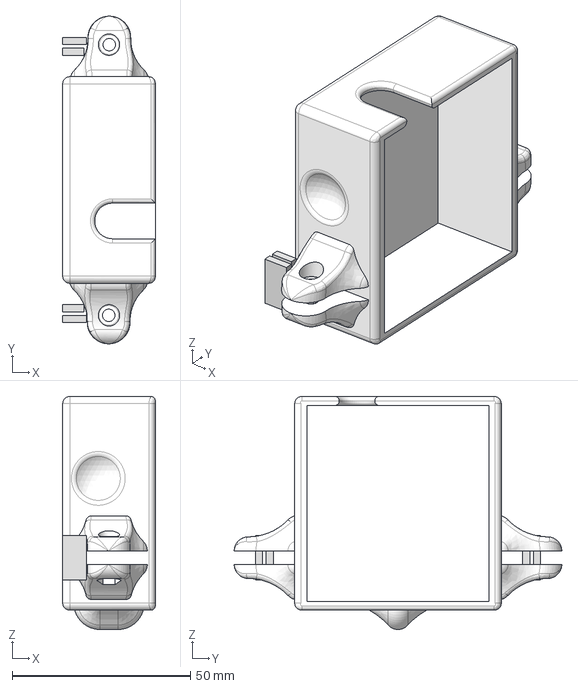
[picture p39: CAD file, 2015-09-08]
Evolution/step/Evolution_porta_portapilas_nuevo_logo.step
26.0 x 92.0 x 65.4 mm

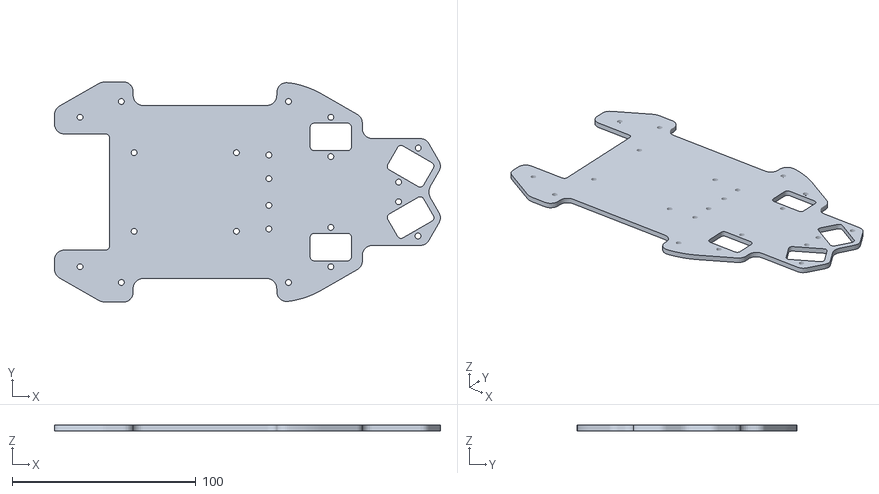
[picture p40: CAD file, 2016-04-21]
Evolution/stl/Evolution_mod_individual_IR_acrylic_3mm_base.stl
210.0 x 119.8 x 3.00

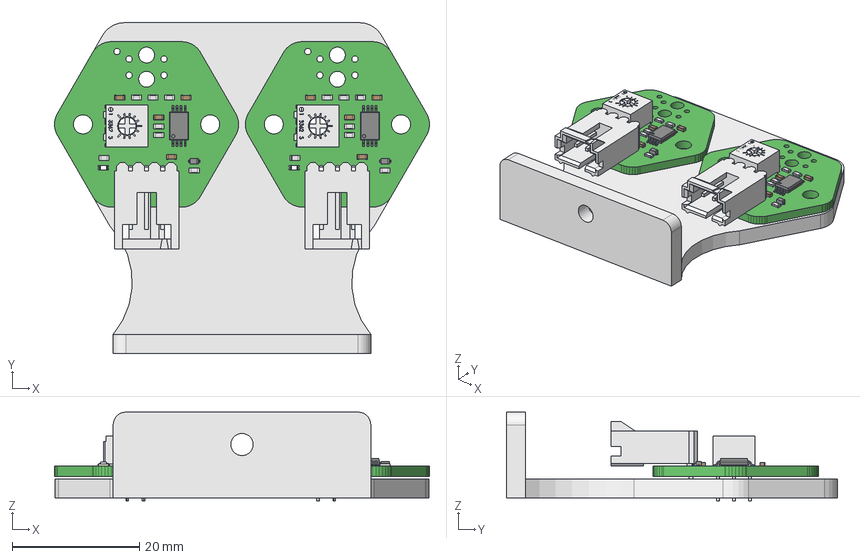
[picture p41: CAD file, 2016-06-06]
Renacuajo/freecad/renacuajo-TwoIR-ZUMBloqs.fcstd
59.0 x 52.0 x 14.0 mm
linefollower_holder
BoardbqZUM_bloqs_Light
User_Library-Bourns_3362P004
User_Library-LED_SMD0603
RES_0603L005
User_Library-Bourns_3362P006
RES_0603L
CAP_0603L002
User_Library-LED_SMD0604
User_Library-SOD523
RES_0603L001
User_Library-Bourns_3362P007
User_Library-Bourns_3362P
RES_0603L002
SW3dPS-JEDEC_MO-153_(TSSOP)
User_Library-LED_SMD0605
User_Library-Bourns_3362P005
User_Library-LED_SMD0607
CAP_0603L003
c-0103634-02-u-3d
CAP_0603L001
CAP_0603L
User_Library-LED_SMD0606
RES_0603L004
User_Library-Bourns_3362P002
User_Library-Bourns_3362P003
User_Library-Bourns_3362P001
RES_0603L003
RES_0603L006
BoardbqZUM_bloqs_Light001
User_Library-Bourns_3362P012
User_Library-LED_SMD0608
RES_0603L012
User_Library-Bourns_3362P014
RES_0603L007
CAP_0603L006
User_Library-LED_SMD0609
User_Library-SOD524
RES_0603L008
User_Library-Bourns_3362P015
User_Library-Bourns_3362P008
RES_0603L009
SW3dPS-JEDEC_MO-153_(TSSOP)001
User_Library-LED_SMD0610
User_Library-Bourns_3362P013
User_Library-LED_SMD0612
CAP_0603L007
c-0103634-02-u-3d001
CAP_0603L005
CAP_0603L004
User_Library-LED_SMD0611
RES_0603L011
User_Library-Bourns_3362P010
User_Library-Bourns_3362P011
User_Library-Bourns_3362P009
RES_0603L010
RES_0603L013

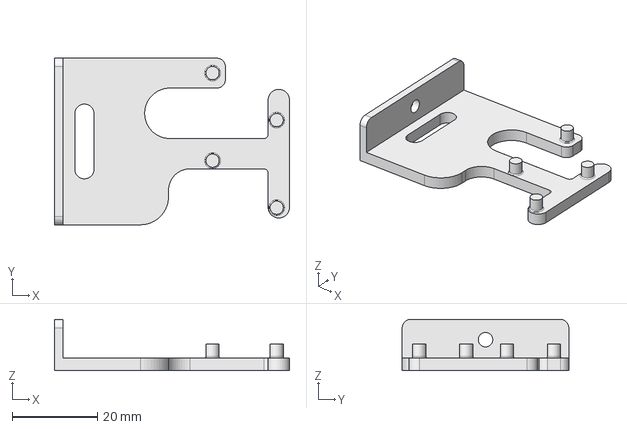
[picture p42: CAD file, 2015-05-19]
Renacuajo/step/renacuajo-snifferV3.step
55.0 x 39.0 x 12.0 mm

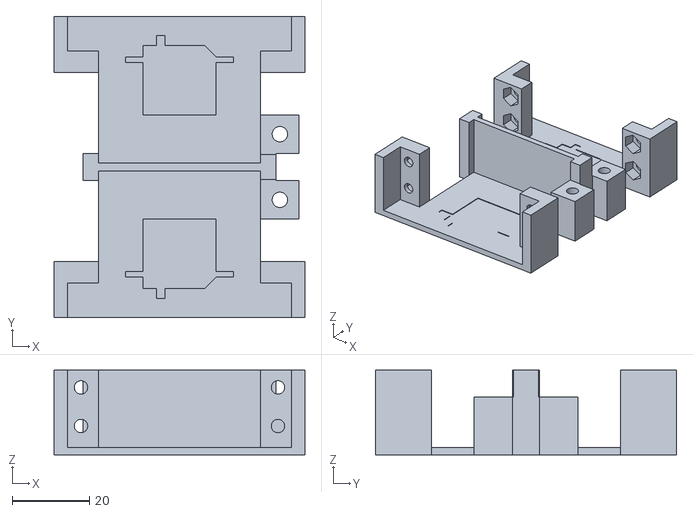
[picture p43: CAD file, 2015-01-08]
Beetle/stl/frame-rear-servo.stl
65.0 x 78.0 x 22.0

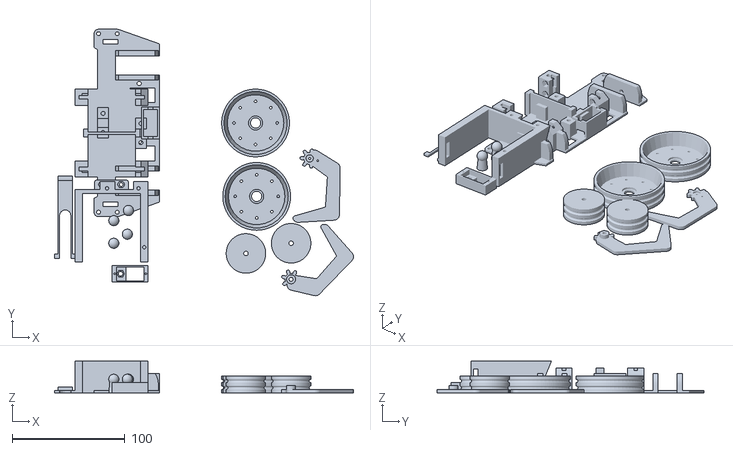
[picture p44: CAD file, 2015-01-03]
Beetle/stl/orig/plate_escarabajo.stl
264.7 x 236.0 x 28.0

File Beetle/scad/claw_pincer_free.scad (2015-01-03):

//ROBOTIC CLAW
//pincer attached to servo
//JGH 17/12/2013

$fn=25;
height=1.5;

translate([0,0,3])	//Orient for printing
rotate([0,180,0])

//GEAR

translate([-1.5,-2.5,3])
rotate ([0,180,0])
include <claw_gear_free.scad>;



translate([0,0,0])	//Orient for printing
//rotate([0,180,0])
		
//PINCER
difference(){
		
		minkowski(){		//everything inside the Minkoski is double the height (I have no idea why)
							//to fix this I set the variable height=1.5 (it should be 3)
			difference(){
				color([0,0,1])
				hull(){
					translate([1, 0, 0])
					cylinder(r=3, h=height);
		
					translate([5, -6, 0])
					cylinder(r=3, h=height);
					
					translate([25, 0, 0])
					cylinder(r=3, h=height);
					
					translate([35, 40, 0])
					cylinder(r=3, h=height);
					
					translate([5, 50, 0])
					cylinder(r=3, h=height);
				}
				
				hull(){
					translate([-6, 0, 0])
					cylinder(r=3, h=height);
					
					translate([20, 10, 0])
					cylinder(r=3, h=height);
					
					translate([25, 35, 0])
					cylinder(r=3, h=height);
					
					translate([0, 50, 0])
					cylinder(r=3, h=height);
				}
			
			}
		
			cylinder(r=2, h=height);
		
		}

	//SAME HOLES AS IN GEAR
	translate([1.5,-2.5,0]){
	color([0,0,1])
	cylinder(r=3.5/2, h=20, $fn=50, center=true);
	
	}
}

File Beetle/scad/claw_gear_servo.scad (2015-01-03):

//////////////////////////////////////////////////////////////////////////////////////////////
// Public Domain Parametric Involute Spur Gear (and involute helical gear and involute rack)
// version 1.1
// by Leemon Baird, 2011, Leemon@Leemon.com
//http://www.thingiverse.com/thing:5505
//
// This file is public domain.  Use it for any purpose, including commercial
// applications.  Attribution would be nice, but is not required.  There is
// no warranty of any kind, including its correctness, usefulness, or safety.
// 
// This is parameterized involute spur (or helical) gear.  It is much simpler and less powerful than
// others on Thingiverse.  But it is public domain.  I implemented it from scratch from the 
// descriptions and equations on Wikipedia and the web, using Mathematica for calculations and testing,
// and I now release it into the public domain.
//
//		http://en.wikipedia.org/wiki/Involute_gear
//		http://en.wikipedia.org/wiki/Gear
//		http://en.wikipedia.org/wiki/List_of_gear_nomenclature
//		http://gtrebaol.free.fr/doc/catia/spur_gear.html
//		http://www.cs.cmu.edu/~rapidproto/mechanisms/chpt7.html
//
// The module gear() gives an involute spur gear, with reasonable defaults for all the parameters.
// Normally, you should just choose the first 4 parameters, and let the rest be default values.
// The module gear() gives a gear in the XY plane, centered on the origin, with one tooth centered on
// the positive Y axis.  The various functions below it take the same parameters, and return various
// measurements for the gear.  The most important is pitch_radius, which tells how far apart to space
// gears that are meshing, and adendum_radius, which gives the size of the region filled by the gear.
// A gear has a "pitch circle", which is an invisible circle that cuts through the middle of each
// tooth (though not the exact center). In order for two gears to mesh, their pitch circles should 
// just touch.  So the distance between their centers should be pitch_radius() for one, plus pitch_radius() 
// for the other, which gives the radii of their pitch circles.
//
// In order for two gears to mesh, they must have the same mm_per_tooth and pressure_angle parameters.  
// mm_per_tooth gives the number of millimeters of arc around the pitch circle covered by one tooth and one
// space between teeth.  The pitch angle controls how flat or bulged the sides of the teeth are.  Common
// values include 14.5 degrees and 20 degrees, and occasionally 25.  Though I've seen 28 recommended for
// plastic gears. Larger numbers bulge out more, giving stronger teeth, so 28 degrees is the default here.
//
// The ratio of number_of_teeth for two meshing gears gives how many times one will make a full 
// revolution when the the other makes one full revolution.  If the two numbers are coprime (i.e. 
// are not both divisible by the same number greater than 1), then every tooth on one gear
// will meet every tooth on the other, for more even wear.  So coprime numbers of teeth are good.
//
// The module rack() gives a rack, which is a bar with teeth.  A rack can mesh with any
// gear that has the same mm_per_tooth and pressure_angle.
//
// Some terminology: 
// The outline of a gear is a smooth circle (the "pitch circle") which has mountains and valleys
// added so it is toothed.  So there is an inner circle (the "root circle") that touches the 
// base of all the teeth, an outer circle that touches the tips of all the teeth,
// and the invisible pitch circle in between them.  There is also a "base circle", which can be smaller than
// all three of the others, which controls the shape of the teeth.  The side of each tooth lies on the path 
// that the end of a string would follow if it were wrapped tightly around the base circle, then slowly unwound.  
// That shape is an "involute", which gives this type of gear its name.
//
//////////////////////////////////////////////////////////////////////////////////////////////

translate([0,0,1.5])

difference(){
	gear();
	cylinder (r=6.5/2, h=1.5, $fn=50);
}

	


//An involute spur gear, with reasonable defaults for all the parameters.
//Normally, you should just choose the first 4 parameters, and let the rest be default values.
//Meshing gears must match in mm_per_tooth, pressure_angle, and twist,
//and be separated by the sum of their pitch radii, which can be found with pitch_radius().
module gear (
	mm_per_tooth    = 6.73,    //this is the "circular pitch", the circumference of the pitch circle divided by the number of teeth
	number_of_teeth = 7,   //total number of teeth around the entire perimeter
	thickness       = 3,    //thickness of gear in mm
	hole_diameter   = 2,    //diameter of the hole in the center, in mm
	twist           = 0,    //teeth rotate this many degrees from bottom of gear to top.  360 makes the gear a screw with each thread going around once
	teeth_to_hide   = 0,    //number of teeth to delete to make this only a fraction of a circle
	pressure_angle  = 28,   //Controls how straight or bulged the tooth sides are. In degrees.
	clearance       = 1,  //gap between top of a tooth on one gear and bottom of valley on a meshing gear (in millimeters)
	backlash        = 1   //gap between two meshing teeth, in the direction along the circumference of the pitch circle
) {
	assign(pi = 3.1415926)
	assign(p  = mm_per_tooth * number_of_teeth / pi / 2)  //radius of pitch circle
	assign(c  = p + mm_per_tooth / pi - clearance)        //radius of outer circle
	assign(b  = p*cos(pressure_angle))                    //radius of base circle
	assign(r  = p-(c-p)-clearance)                        //radius of root circle
	assign(t  = mm_per_tooth/2-backlash/2)                //tooth thickness at pitch circle
	assign(k  = -iang(b, p) - t/2/p/pi*180) {             //angle to where involute meets base circle on each side of tooth
		difference() {
			for (i = [0:number_of_teeth-teeth_to_hide-1] )
				rotate([0,0,i*360/number_of_teeth])
					linear_extrude(height = thickness, center = true, convexity = 10, twist = twist)
						polygon(
							points=[
								[0, -hole_diameter/10],
								polar(r, -181/number_of_teeth),
								polar(r, r<b ? k : -180/number_of_teeth),
								q7(0/5,r,b,c,k, 1),q7(1/5,r,b,c,k, 1),q7(2/5,r,b,c,k, 1),q7(3/5,r,b,c,k, 1),q7(4/5,r,b,c,k, 1),q7(5/5,r,b,c,k, 1),
								q7(5/5,r,b,c,k,-1),q7(4/5,r,b,c,k,-1),q7(3/5,r,b,c,k,-1),q7(2/5,r,b,c,k,-1),q7(1/5,r,b,c,k,-1),q7(0/5,r,b,c,k,-1),
								polar(r, r<b ? -k : 180/number_of_teeth),
								polar(r, 181/number_of_teeth)
							],
 							paths=[[0,1,2,3,4,5,6,7,8,9,10,11,12,13,14,15,16]]
						);
			cylinder(h=2*thickness+1, r=hole_diameter/2, center=true, $fn=20);
		}
	}
};	
//these 4 functions are used by gear
function polar(r,theta)   = r*[sin(theta), cos(theta)];                            //convert polar to cartesian coordinates
function iang(r1,r2)      = sqrt((r2/r1)*(r2/r1) - 1)/3.1415926*180 - acos(r1/r2); //unwind a string this many degrees to go from radius r1 to radius r2
function q7(f,r,b,r2,t,s) = q6(b,s,t,(1-f)*max(b,r)+f*r2);                         //radius a fraction f up the curved side of the tooth 
function q6(b,s,t,d)      = polar(d,s*(iang(b,d)+t));                              //point at radius d on the involute curve

//a rack, which is a straight line with teeth (the same as a segment from a giant gear with a huge number of teeth).
//The "pitch circle" is a line along the X axis.
module rack (
	mm_per_tooth    = 3,    //this is the "circular pitch", the circumference of the pitch circle divided by the number of teeth
	number_of_teeth = 11,   //total number of teeth along the rack
	thickness       = 6,    //thickness of rack in mm (affects each tooth)
	height          = 120,   //height of rack in mm, from tooth top to far side of rack.
	pressure_angle  = 28,   //Controls how straight or bulged the tooth sides are. In degrees.
	backlash        = 0.0   //gap between two meshing teeth, in the direction along the circumference of the pitch circle
) {
	assign(pi = 3.1415926)
	assign(a = mm_per_tooth / pi) //addendum
	assign(t = a*cos(pressure_angle)-1)         //tooth side is tilted so top/bottom corners move this amount
		for (i = [0:number_of_teeth-1] )
			translate([i*mm_per_tooth,0,0])
				linear_extrude(height = thickness, center = true, convexity = 10)
					polygon(
						points=[
							[-mm_per_tooth * 3/4,                 a-height],
							[-mm_per_tooth * 3/4 - backlash,     -a],
							[-mm_per_tooth * 1/4 + backlash - t, -a],
							[-mm_per_tooth * 1/4 + backlash + t,  a],
							[ mm_per_tooth * 1/4 - backlash - t,  a],
							[ mm_per_tooth * 1/4 - backlash + t, -a],
							[ mm_per_tooth * 3/4 + backlash,     -a],
							[ mm_per_tooth * 3/4,                 a-height],
						],
						paths=[[0,1,2,3,4,5,6,7]]
					);
};
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

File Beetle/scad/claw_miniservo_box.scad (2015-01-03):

//ROBOTIC CLAW
//For mini servo EMax ES08A
//JGH 16/12/2013

translate([0,0,9])	//orient for printing
rotate([180,0,0])

difference(){
	cube ([32, 15, 9]);			//Main box
	
	translate([12.2, 1.3, 0])	//Area for round parts
	color([1,1,1])
	cube ([16, 12.4, 9]);
	
	translate([3.8, 1.3, 0])		//Area fo square section of servo
	color([0,0,1])
	cube ([24.4, 12.4, 4.8]);

	translate([7.6, 7.5, 3.8])		//Hole for 3M nut
	cylinder(r=3.4, h=4.1, $fn=6);

	translate([7.6, 7.5, 3.8])		//Hole for 3M screw
	cylinder(r=2, h=10, $fn=25);

	translate([2.3, 7.5, 0])			//Holes for underside M2 screws
	cylinder(r=1, h=8, $fn=6);

	translate([29.7, 7.5, 0])
	cylinder(r=1, h=8, $fn=6);
}

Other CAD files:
Evolution/addons/guardabarros_con_sensor/stl/guardabarros_con_sensor.stl
Beetle/step/frame-front.step
Evolution/addons/bumper/stl/final_bumper_rounded_evolution.stl
Evolution/step/Evolution_cuerpo_V2.step
Beetle/scad/claw_pincer_servo.scad
Beetle/freecad/battery-pack-clip.fcstd
Beetle/freecad/battery-pack-holder.fcstd
Beetle/freecad/claw-miniservo-box.fcstd
Beetle/freecad/claw-pincer-free.fcstd
Beetle/freecad/claw-pincer-servo.fcstd
Beetle/freecad/frame-front.fcstd
Beetle/freecad/frame-rear-servos.fcstd
Beetle/freecad/servo-screw-cover.fcstd
Beetle/freecad/wheel-front.fcstd
Beetle/freecad/wheel-rear.fcstd
Beetle/legacy/v1.0/scad/SM-S4303R.scad
Beetle/legacy/v1.0/scad/assembly.scad
Beetle/legacy/v1.0/scad/battery_pack_clip.scad
Beetle/legacy/v1.0/scad/battery_pack_holder.scad
Beetle/legacy/v1.0/scad/claw_gear_free.scad
Beetle/legacy/v1.0/scad/claw_pincer_servo.scad
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

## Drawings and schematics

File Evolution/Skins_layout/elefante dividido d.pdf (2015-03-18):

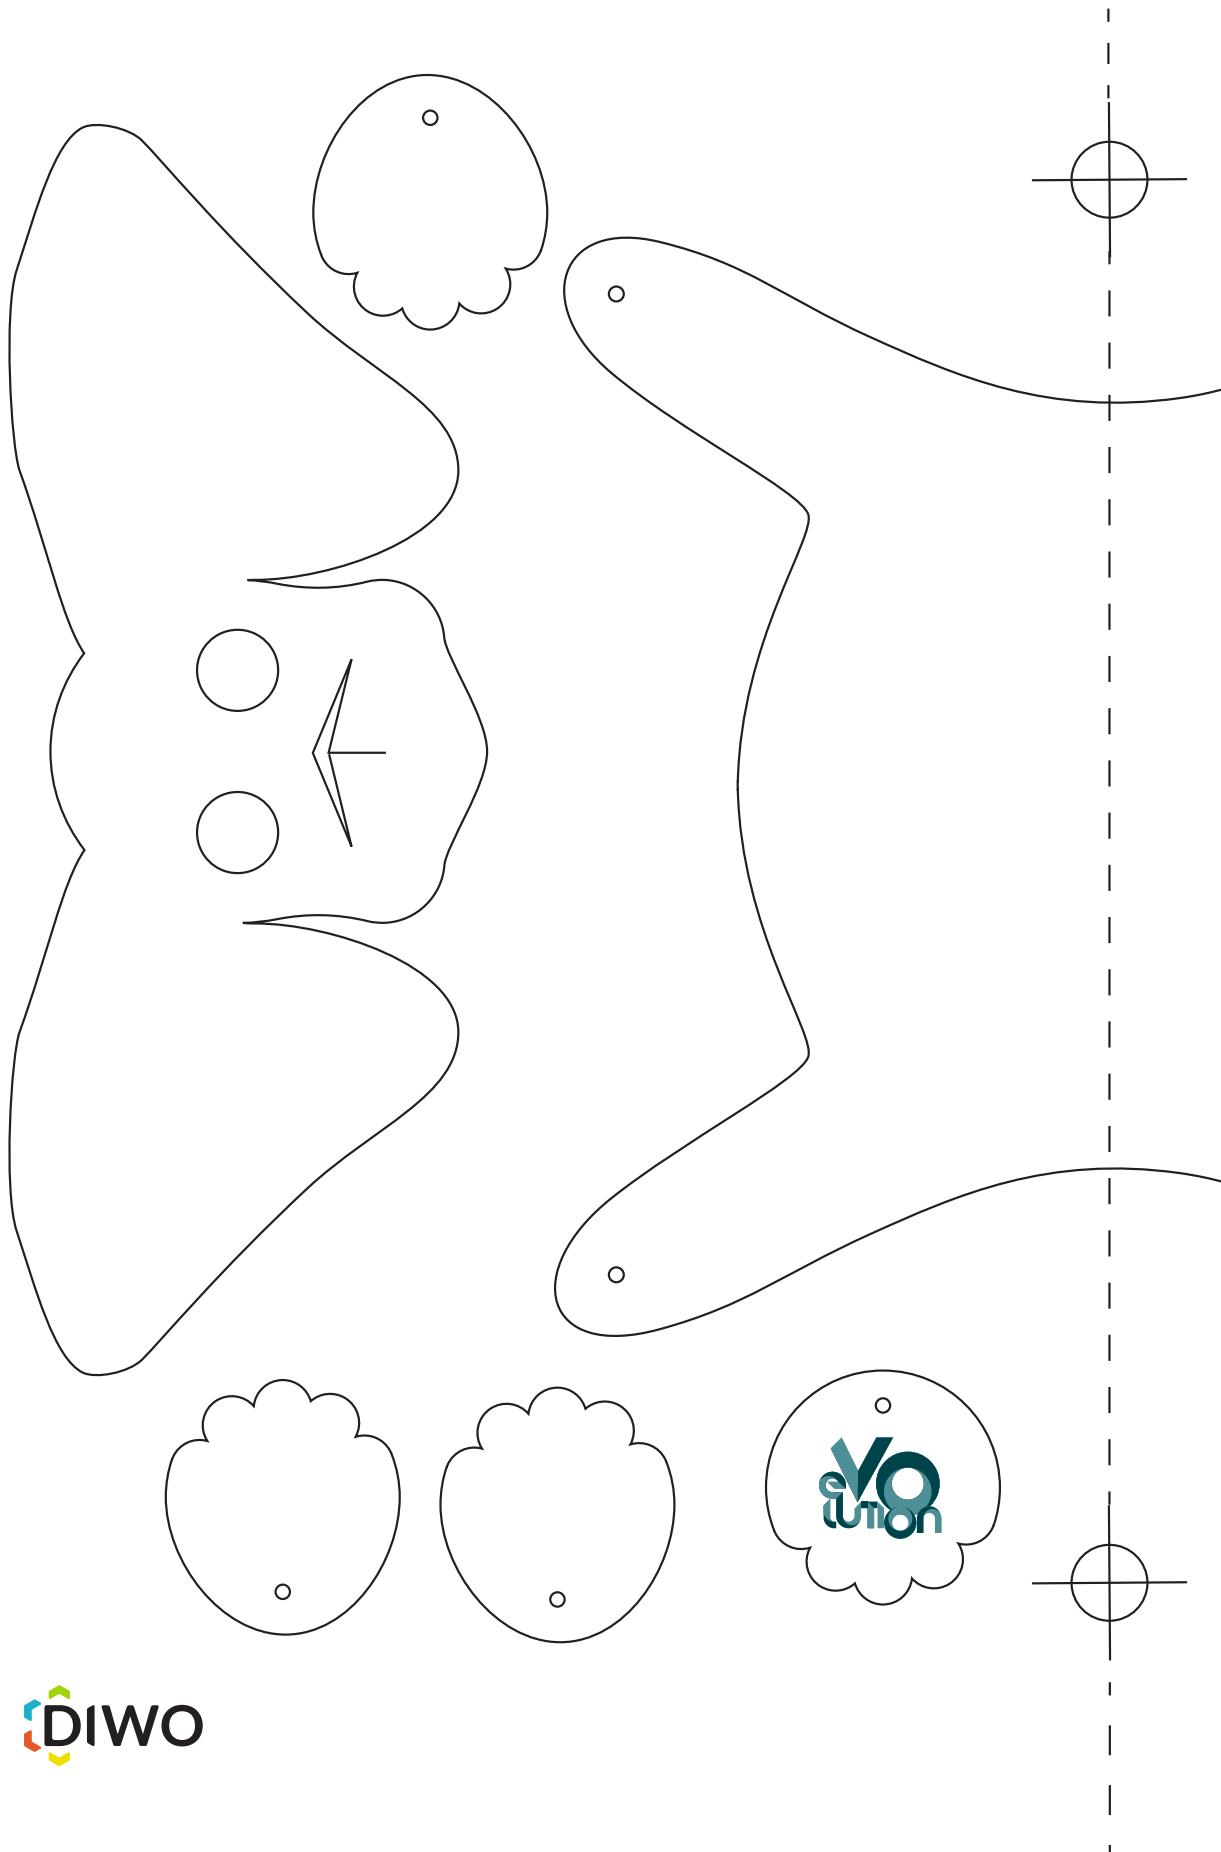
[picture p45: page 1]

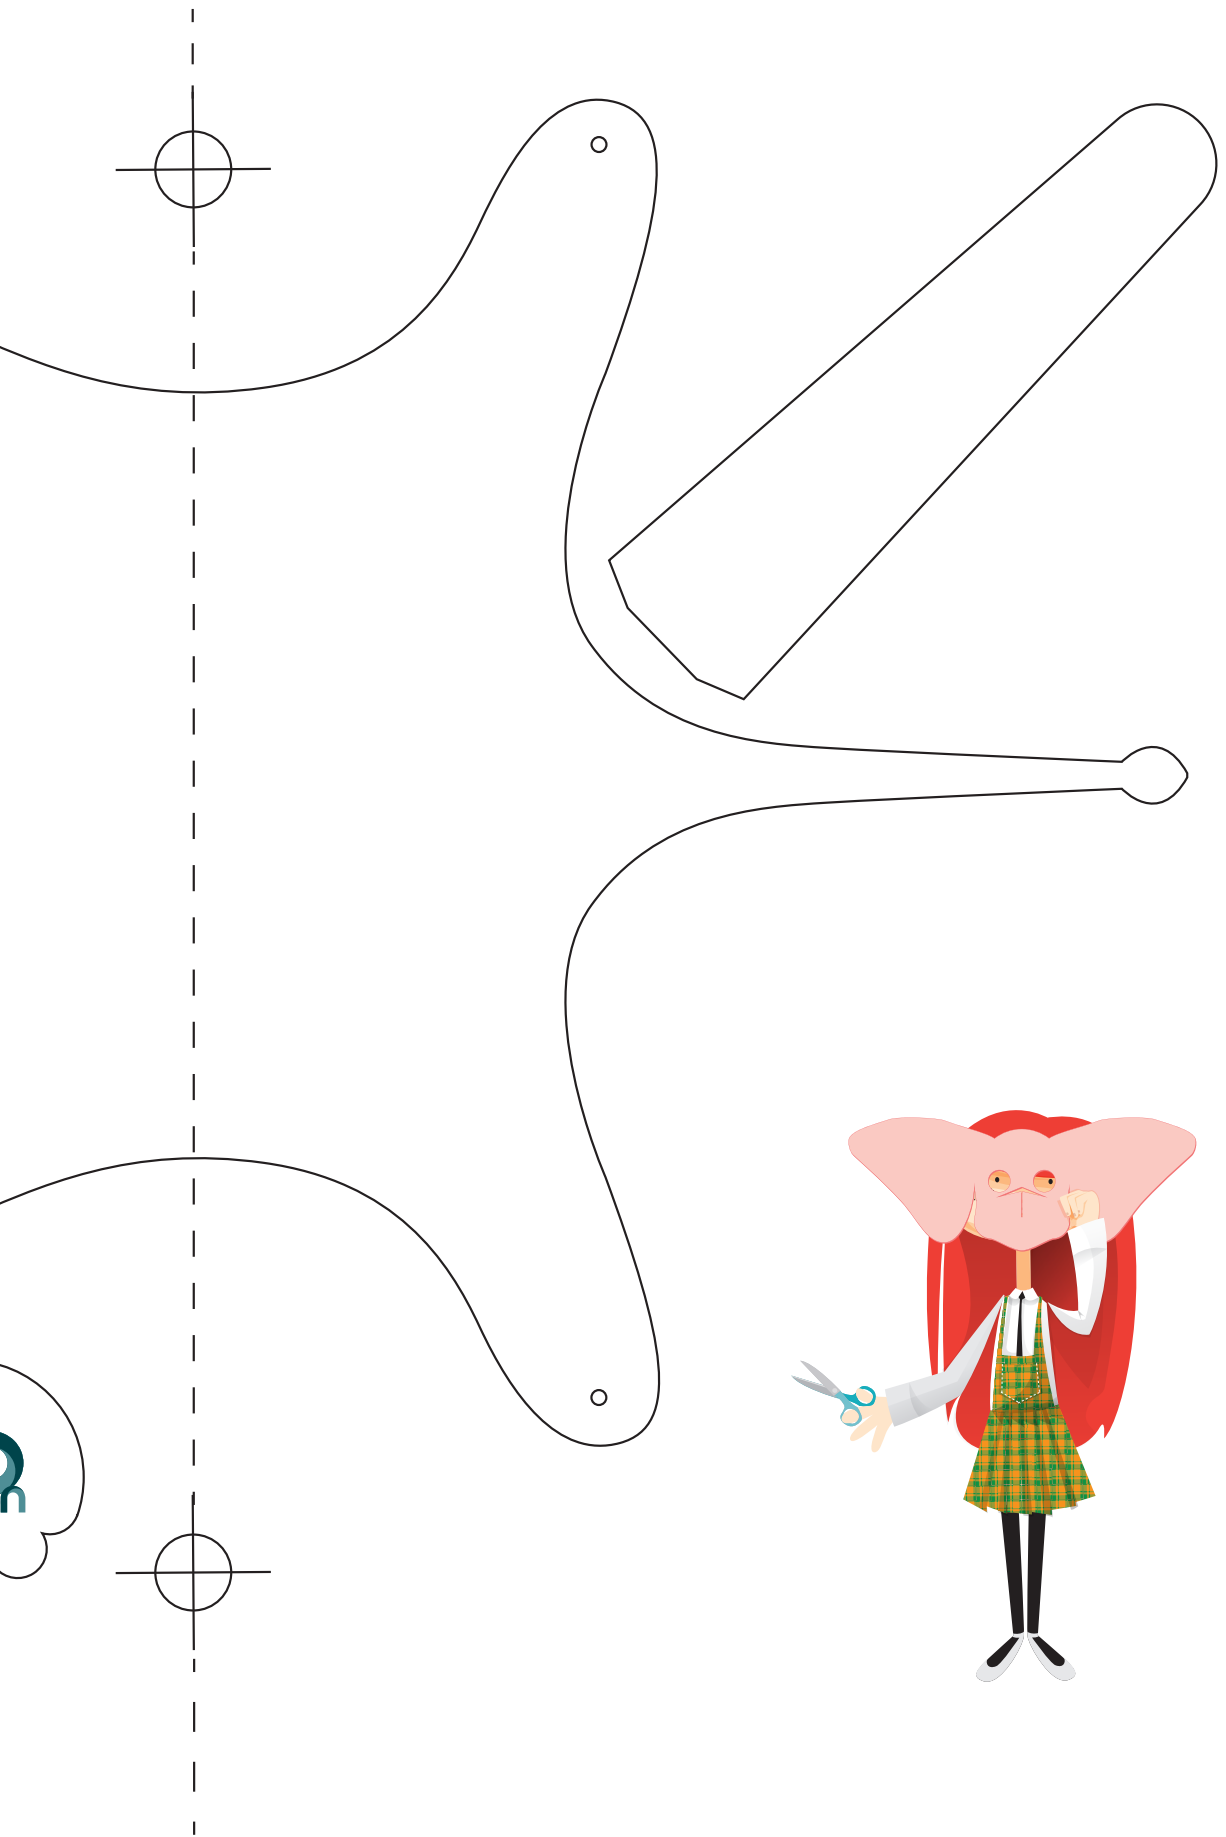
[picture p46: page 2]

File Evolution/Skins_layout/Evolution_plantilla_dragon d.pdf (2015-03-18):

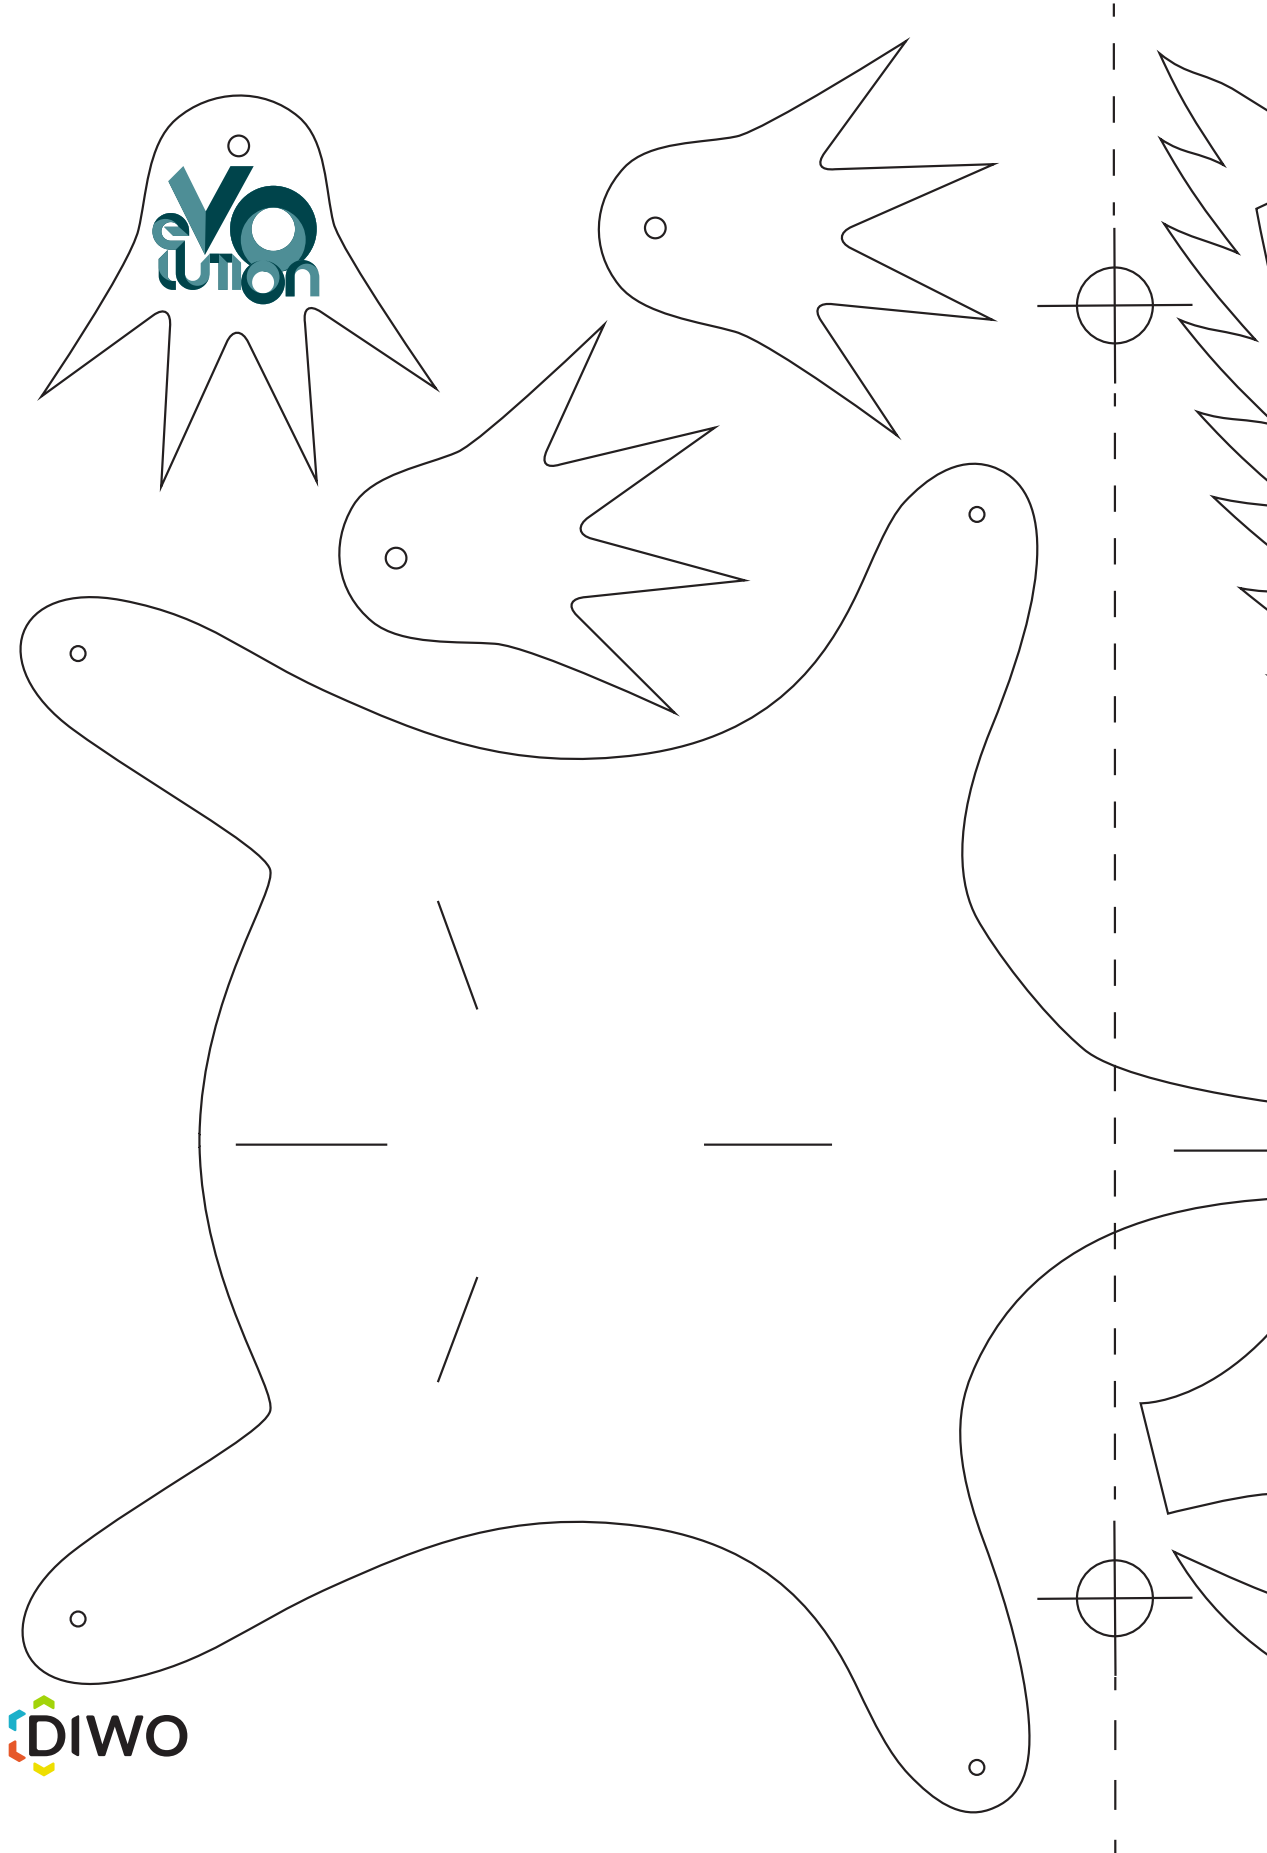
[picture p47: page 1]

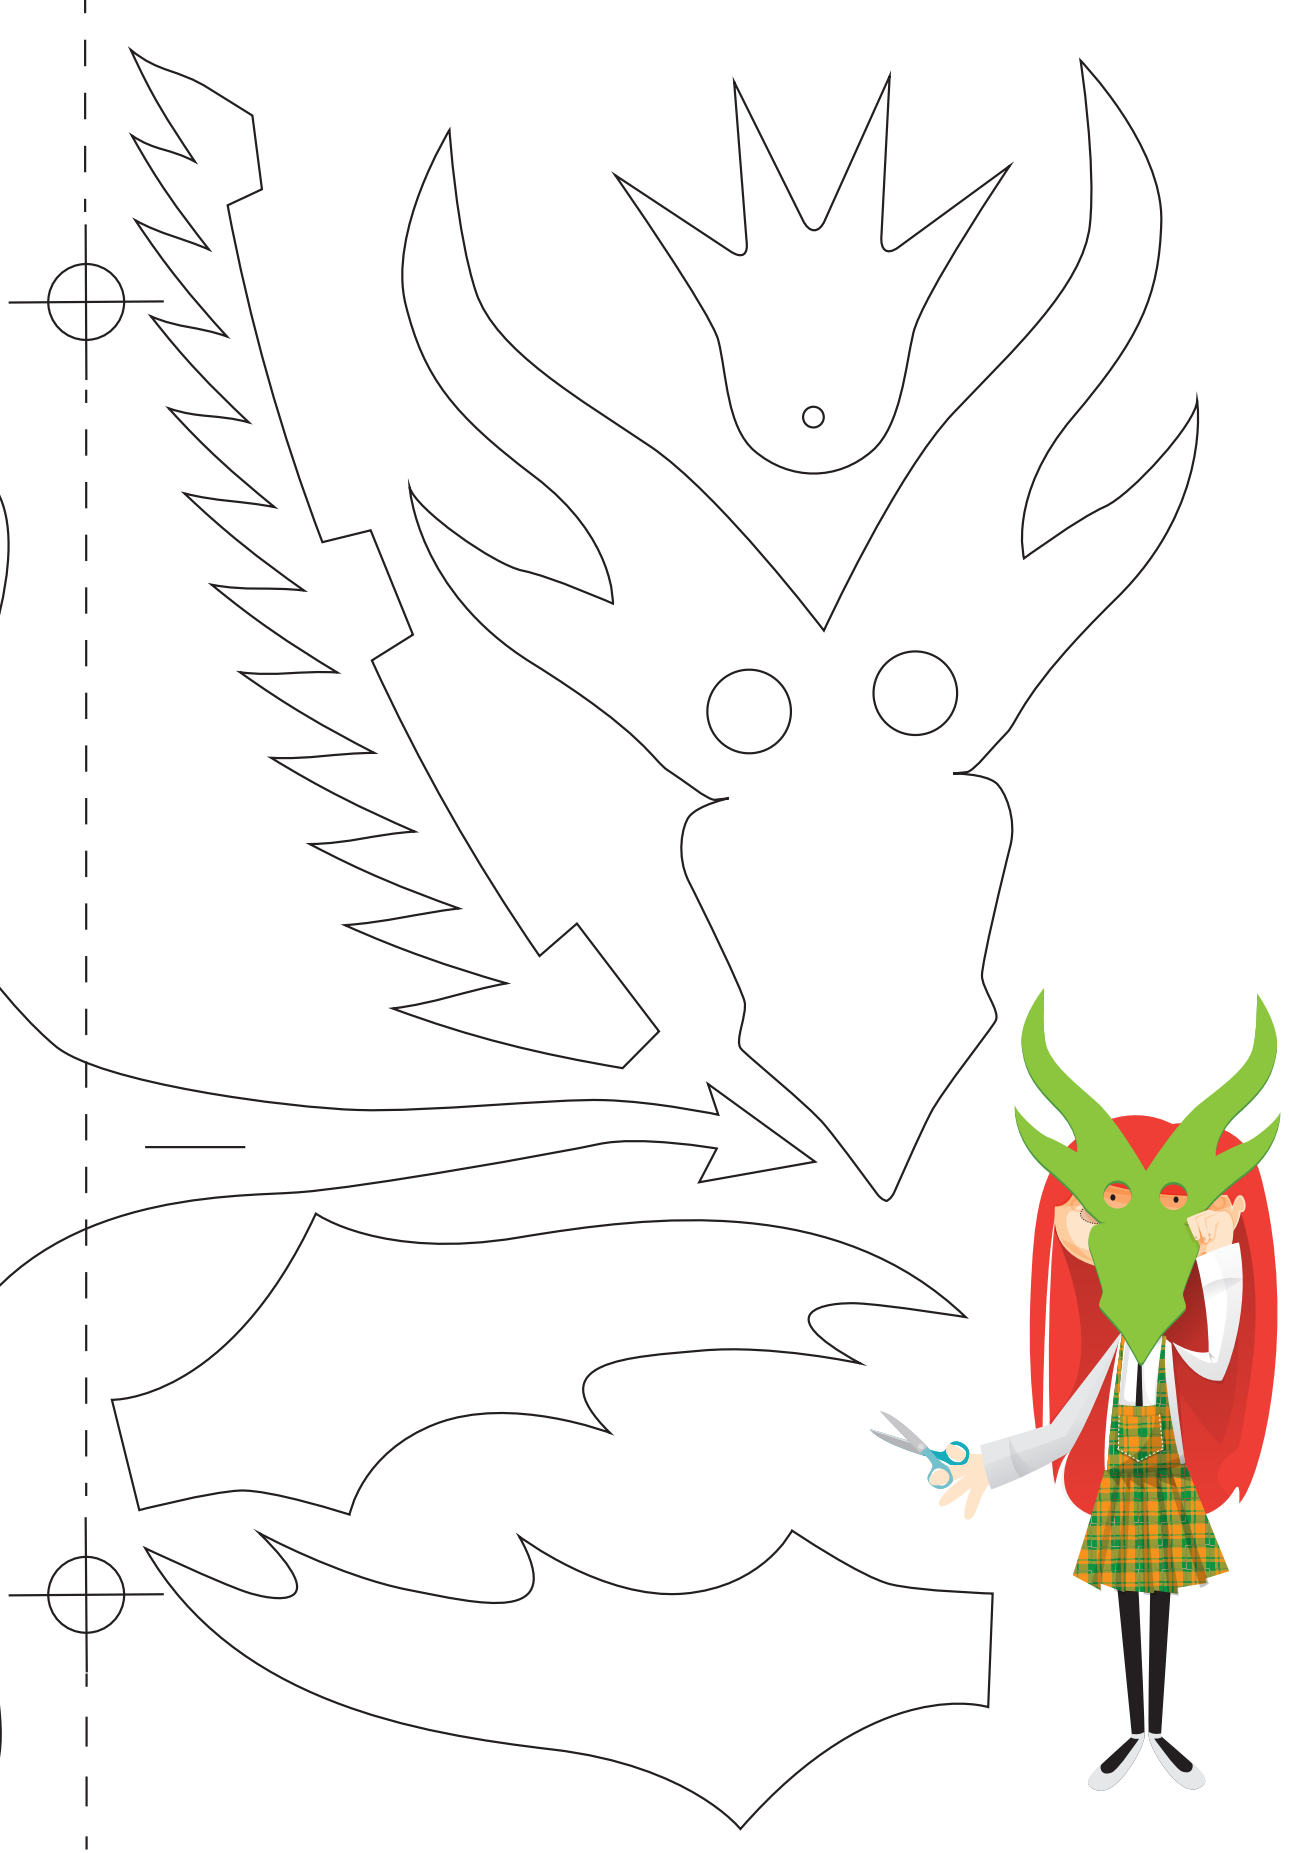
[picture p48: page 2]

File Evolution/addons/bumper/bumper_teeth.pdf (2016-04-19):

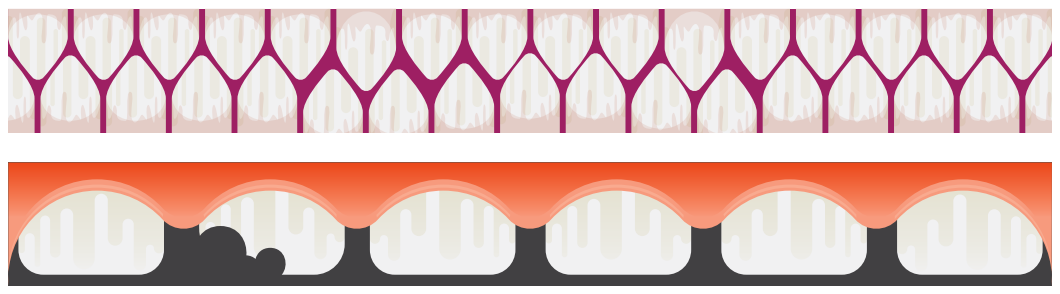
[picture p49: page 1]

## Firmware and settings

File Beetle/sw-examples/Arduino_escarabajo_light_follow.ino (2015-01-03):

#include <Servo.h>

Servo servoR;
Servo servoL;
Servo claw;

const int SL = A5;    // the number of the left sensor pin
const int SR= A4;     // the number of the right sensor pin

//-- Right and left IR sensors values
int rs,ls;

const int BLACK = 0;
const int WHITE = 1;


void setup(){
  pinMode(SL, INPUT);
  pinMode(SR, INPUT);
  enable();
}

void loop(){
  rs = analogRead(SR);
  ls= analogRead(SL);

//-- Move the robot according to the inputs
  if (abs(ls-rs)<20){ 
     move_Forward();
     claw.write(3); 
     delay(10);
  }  

  else if (ls > rs){  
     move_Left();
     claw_close(); 
  }  

  else if (ls < rs){
     move_Right();
     claw_open(); 
  }  
  
  else{ 
     Stop();
     
  }
}


void enable(){
  
   servoR.attach(9);  
   servoL.attach(10);
   claw.attach(4);
    
   servoL.write(90);
   servoR.write(90);
   claw.write(3);
}


void Stop(){
  
   servoL.write(90);
   delay(10);
   servoR.write(90);
   delay(10);
}

void move_Forward(){

    servoL.write(0);
    delay(10);
    servoR.write(180);
    delay(10);
}

void move_Back(){
  
    servoL.write(180);
    delay(10);
    servoR.write(0);
    delay(10);
}

void move_Right(){

    servoL.write(0);
    delay(10);
    servoR.write(90);
    delay(10); 
}

void move_Left(){

   servoL.write(90);
   delay(10);
   servoR.write(180);
   delay(10);
}

void claw_open(){
  claw.write(3);
}

void claw_close(){
  claw.write(50);
}

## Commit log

2014-09-27 Renacuajo chassis: half base
    [renacuajo-chassis.fcstd, renacuajo-chassis.stl]
2014-09-28 Half right base: printed and tested. ok
    [renacuajo-chassis.fcstd]
2014-09-28 Renacuajo chassis: first draft. Not yet tested
    [renacuajo-chassis.fcstd]
2014-09-30 Servos added. Chassis printed and tested
    [renacuajo-chassis.fcstd]
2014-10-03 renacuajo chassis: stl file printed ok
    [renacuajo-chassis.stl]
2014-10-04 Chassis: freecad file cleaned
    [renacuajo-chassis.fcstd]
2014-10-04 Renacuajo assembly: chassis, servos and wheels
    [renacuajo-assembly.fcstd]
2014-10-04 chassis: height of the caster wheel reduced in 2.6mm. Not yet tested
    [renacuajo-chassis.fcstd]
2014-10-04 Renacuajo chassis. Small changes
    [renacuajo-chassis.fcstd]
2014-10-04 renacuajo battery holder: first draft. Not yet printed
    [renacuajo-battery-holder.fcstd, renacuajo-battery-holder.stl]
2014-10-04 Renacuajo sniffer: first draft. Not yet tested
    [renacuajo-sniffer.fcstd, renacuajo-sniffer.stl]
2014-10-04 Renacuajo chassis: new stl for printing and testing
    [renacuajo-chassis.stl]
2014-10-04 Renacuajo sniffer: simple copy added. Sniffer printed and tested
    [renacuajo-sniffer.fcstd]
2014-10-04 Renacuajo battery holder: model cleaned
    [renacuajo-battery-holder.fcstd]
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2014-10-05 Wheels added from the printbot library
    [Renacuajo-original-wheel-screws.fcstd]
2014-10-05 Renacuajo: step and stl files
    [renacuajo-battery-holder.step, renacuajo-chassis.step, renacuajo-original-wheel-screws.step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]
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2014-12-30 stl original files moved to the stl/orig folder
    [battery_pack_clip.stl, battery_pack_holder.stl, claw_miniservo_box.stl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]
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2015-01-05 battery pack holder migrated to freecad. Ready to be tested
    [battery-pack-holder.fcstd, battery-pack-holder.stl]
2015-01-07 frame rear servo: connector with the front part reduced in 0.2mm
    [frame-rear-servo.stl, frame-rear-servos.fcstd]
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2015-01-08 Frame rear servo: Frontal male connector length set to 6.5mm instead of 6.8. Now both the frame front and the fron rear should fit better
    [frame-rear-servo.step, frame-rear-servo.stl, frame-rear-servos.fcstd]
2015-01-08 Frame front: Ir and LDR sensors added, with their bolts and nuts
    [Assembly.fcstd]
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2015-01-10 clar miniservo box migrated to freecad. First draft
    [claw-miniservo-box.fcstd, claw-miniservo-box.step, claw-miniservo-box.stl]
2015-01-11 Claw pincer servo modified. Horn drill made bigger: 0.75mm radius
    [claw-pincer-servo.fcstd, claw-pincer-servo.step, claw-pincer-servo.stl]
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2015-01-11 Assembly: battery pack and battery pack clib added
    [Assembly.fcstd]
2015-01-12 wheel rear migrated to freecad (by David Sanchez)
    [wheel-rear.fcstd, wheel-rear.step, wheel_rear.stl]
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2015-01-13 Frame front: ir sensors moved 4mm to the front. Base increased in 4mm. Part restructured
    [frame-front.fcstd]
2015-01-13 Top drills new radius: from 1.57 --> 1.55mm. With 1.57 bolts were too loose
    [battery-pack-holder.fcstd, battery-pack-holder.step, battery-pack-holder.stl]
2015-01-13 frame front: slot added in the bottom for passing the mini servo wires
    [frame-front.fcstd, frame-front.step, front-frame.stl]
2015-01-13 Added some space in the battery pack holder for the wires
    [battery-pack-holder.fcstd, battery-pack-holder.step, battery-pack-holder.stl]
2015-01-13 Battery pack: another cutout for wires in the right side
    [battery-pack-holder.fcstd, battery-pack-holder.step, battery-pack-holder.stl]
2015-01-13 Assembly: battery pack holder updated to the newest version
    [Assembly.fcstd]
2015-01-14 batery pack holder place on the top of z=0 plane
    [battery-pack-holder.fcstd, battery-pack-holder.step, battery-pack-holder.stl]
2015-01-14 battery pack holder: side slots increased in 0.4mm
    [battery-pack-holder.fcstd, battery-pack-holder.step, battery-pack-holder.stl]
2015-01-14 frame front: 2mm offset in z so that it is placed on the z=0 plane
    [frame-front.fcstd, frame-front.step, front-frame.stl]
2015-01-15 Battery pack holder: modification by David Sanchez added
    [battery-pack-holder.fcstd, battery-pack-holder.step, battery-pack-holder.stl]
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2015-02-04 Beetle: M3x10 bolts added for attaching the electronics
    [Assembly.fcstd]
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2015-02-05 legacy folder created with version 1 of the Beetle printbot
    [SM-S4303R.scad, assembly.scad, battery_pack_clip.scad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]
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2015-02-16 Renacuajo: freecad files moved to the freecad folder
    [Renacuajo-original-wheel-screws.fcstd, renacuajo-DoubleIR-tongue.fcstd, renacuajo-assembly.fcstd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]
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2015-04-15 Sniffer updated. There were problems with some sensors, that are a little bigger than initially. It has been fixed
    [renacuajo-sniffer.fcstd, renacuajo-sniffer.step, renacuajo-sniffer.stl]
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2016-04-19 Added a mod acrylic base that use 2 individuals IR- By Jokin Lacalle
    [Evolution_mod_individual_IR_acrylic_3mm_base.dxf]
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2016-04-21 Added the stl for the modded base with individuals IR
    [Evolution_mod_individual_IR_acrylic_3mm_base.stl]
2016-06-06 Added files for another version of the linefollower with two ZumBloqs IR-Created by Fernando Coladas Rodríguez
    [renacuajo-TwoIR-ZUMBloqs.fcstd, renacuajo-TwoIR-ZUMBloqs.stl]
2016-08-12 Added a new addon, now you can put ZUM sensors in the cover wheels
    [guardabarros_con_sensor.stl, guardabarros_ir_adaptador_evolution_up.fcstd]
